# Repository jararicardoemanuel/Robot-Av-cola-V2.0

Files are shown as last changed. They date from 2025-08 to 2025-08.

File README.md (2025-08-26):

<h1 align="center" style="color:brown;">
  🐔🥚Robot Avícola V2.0
</h1>

Proyecto de la Práctica Profesional Supervisada "PPS" en Ingeniería Mecatrónica realizado en la FI-UNLZ.

Es un sistema robótico de 3 GDL para realizar la recolección de huevos en nidos horizontales, tiene implementado un software de procesamiento de imágenes para la detección y localización programado en python utilizando la librería cv2 y un modelo pre-entrenado de roboflow. Se emplea un Sistema IoT para el accionamiento de control, aplicación para el envío de mensajes y recepción a través de "MQTT", además del monitoreo de variables ambientales cómo la temperatura, gas CO2, húmedad.

<p align="center">
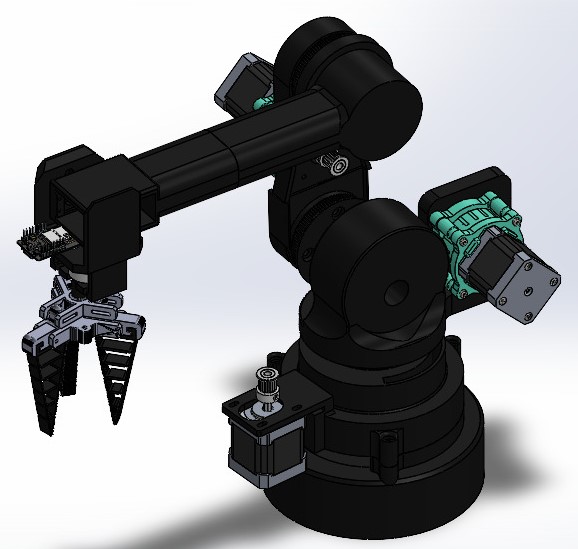
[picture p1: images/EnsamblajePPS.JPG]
  
</p>

## 🟠Tecnologías Aplicadas
• ESP32 - Shield cnc 3 ejes, para el robot se utilizan motores nema 17 con reductor planetario 5:1, motores eléctricos de cc para el carro que lo traslada y sensores de proximidad FC.
• Python - OpenCV, para el diseño de software de detección y calculo de la cinemática inversa.
• Node-RED - MQTT, para el envío y recepción de mensajes, aplicando los nodos se diseño un dashboard de control y monitoreo.
• Sensores de CO₂ MQ135, temperatura y humedad DHT11

## 🟠Prototipo REAL

<p align="center">
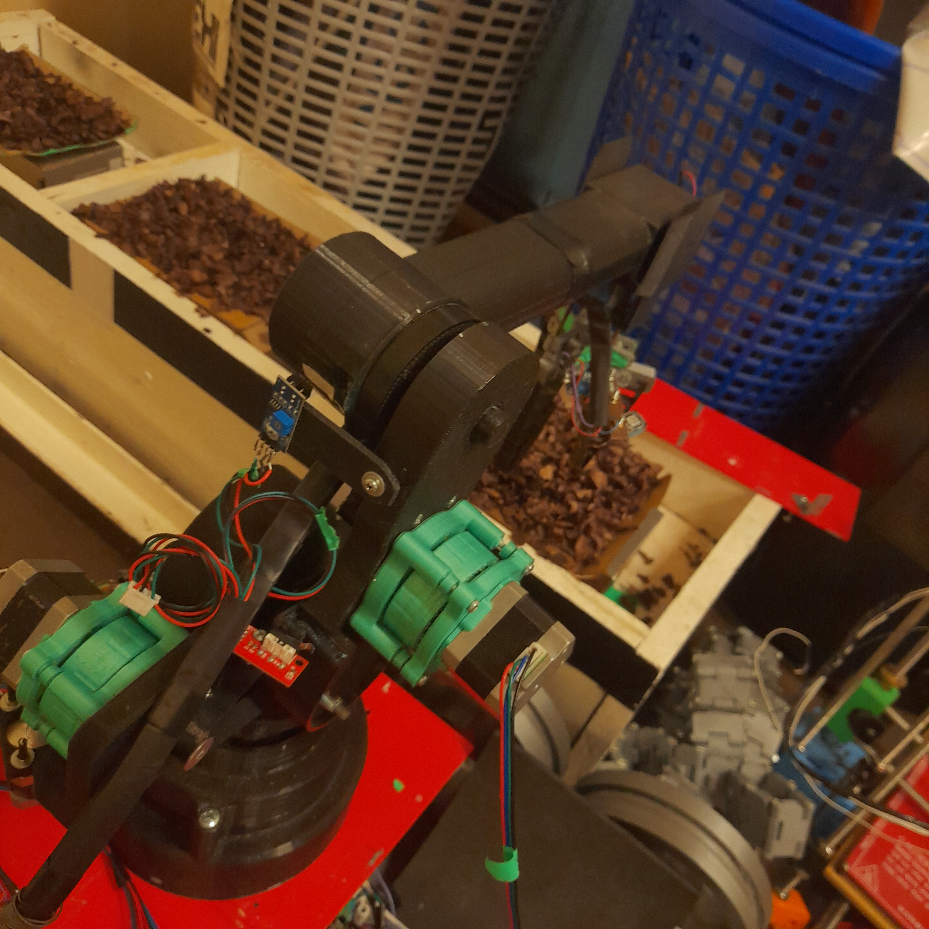
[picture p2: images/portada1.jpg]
  
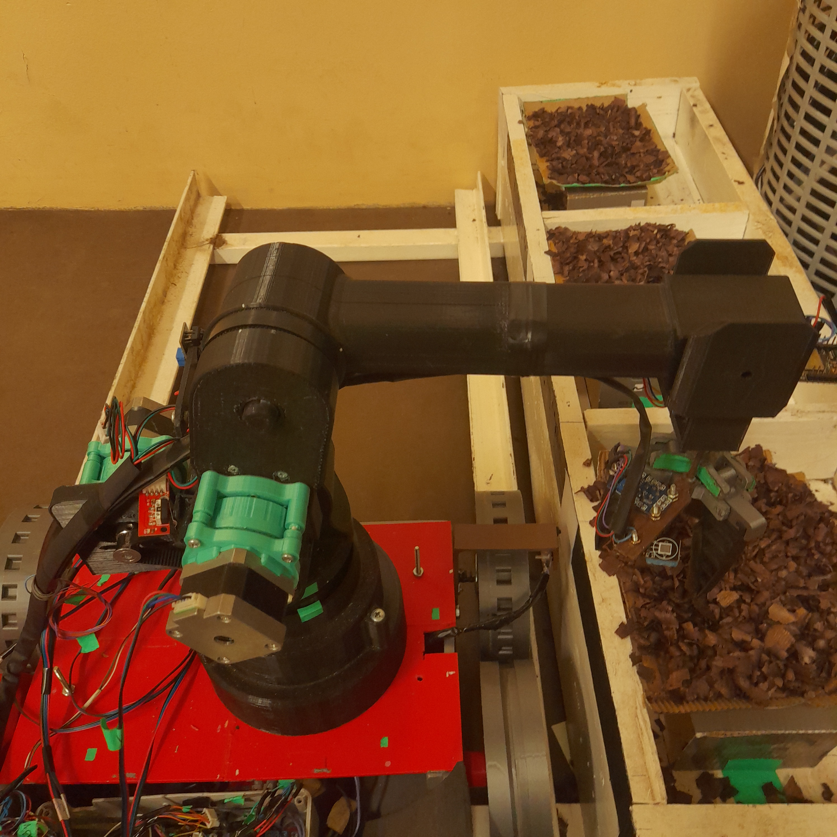
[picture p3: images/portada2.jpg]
  
</p>

## 🟠Procesamiento de Imágenes

Para la detección automática de huevos se utiliza un modelo de visión por computadora entrenado en la plataforma Roboflow. El flujo de trabajo se resume en las siguientes etapas:

### Captura de imagen:
  La cámara ESP32-CAM ubicada en el extremos del codo apuntando hacia abajo captura las imágenes en tiempo real enfocando el nido cubriendo toda la parte donde se ubica el huevo.
  La foto lo comprime en formato JPEG. Este archivo se transfiere a la PC. El resultado de este paso es un archivo ".jpg" accesible en el host.
### Inferencia con el modelo:
  Las imágenes capturadas son enviadas al modelo de Roboflow, el cual aplica un algoritmo de detección de objetos (YOLOv9). Como resultado, se obtiene un conjunto de predicciones que      incluyen:
  Clases detectadas (``huevo'').
  Confianza de detección (probabilidad asociada a la predicción).
  Coordenadas del recuadro:
  (x, y, w, h) donde $x$ e $y$ representan la posición central del objeto, mientras que $w$ y $h$ corresponden al ancho y alto del recuadro.

### Conversión a coordenadas del robot:
  A partir de las coordenadas $(x, y)$ obtenidas de la imagen (resolución de $640 \times 480$ píxeles), se realiza una transformación a coordenadas físicas reales del robot:
  (X_r, Y_r) quedando en función de f (x,y) del sistema
  donde la función $f$ corresponde a la calibración que traduce los píxeles en coordenadas cartesianas, garantizando que el brazo robótico pueda posicionarse correctamente sobre el        huevo.

  • Conversión de píxeles a coordenadas físicas:

En el sistema de visión, las detecciones entregadas por el modelo de Roboflow
se expresan en coordenadas de imagen en píxeles. Para utilizar estos
datos en el control del robot, es necesario transformarlos a coordenadas físicas
(X,Y) medidas en centímetros sobre el plano de trabajo.

En una aproximación simple, se realiza una calibración lineal por
ejes independientes, donde se ajusta un factor de escala y un desplazamiento
(offset) a partir de puntos de referencia medidos experimentalmente:

$$
X = a_x \cdot u + b_x, \qquad
Y = a_y \cdot v + b_y
$$

donde:

  •  \(u,v\): coordenadas en píxeles de la detección
  
  •  \(X,Y\): coordenadas físicas en cm
  
  •  \(a_x, a_y\): factores de conversión (cm/px)
  
  •  \(b_x, b_y\): offsets de calibración

En el prototipo actual se obtuvieron los siguientes valores:

$$
X = (0.0328)\cdot u + 0.5, \qquad
Y = (0.0327)\cdot v + 0.3
$$

### Selección y validación:
  Se consideran válidas únicamente las detecciones cuyo nivel de confianza sea mayor a un umbral predefinido $0.40$. 
    
### Envío al sistema de control:
  Finalmente, con las coordenadas cartesianas corregidas $(X_r, Y_r)$ se calcula la cinemática inversa por método geométrico del robot RRR para luego transmitir los angulos por el protocolo MQTT al controlador del robot para luego ejecutar la secuencia de agarre y recolección.

  La salida del modelo Roboflow
  La predicción para un huevo detectado es el siguiente:
  "predictions": 
      "class": "egg",
      "confidence": 0.89,
      "x": 320,
      "y": 240,
      "width": 50,
      "height": 60
Este resultado indica que se detectó un huevo con una confianza del $0.89$ en la posición $(320, 240)$. Se adjuntan imagenes dónde se observa la localización del objeto y como son transmitidas a través de mqtt.

<p align="center">
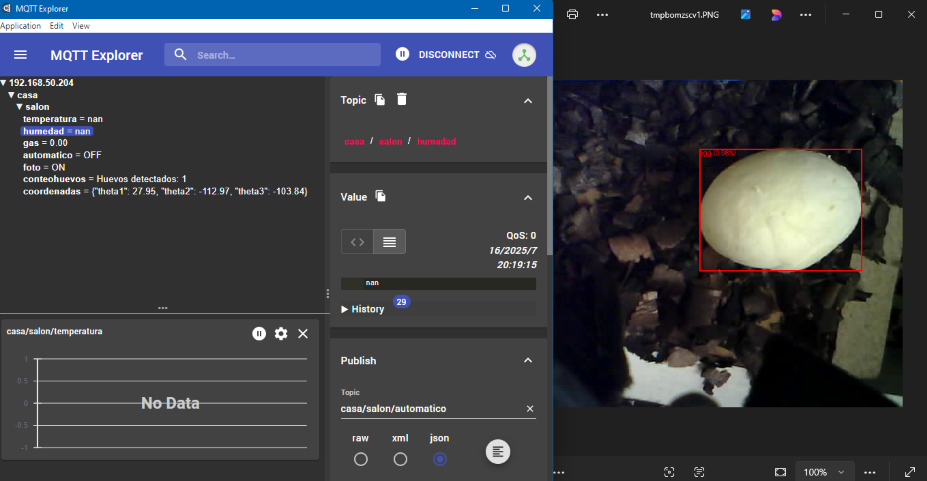
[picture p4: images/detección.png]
  
</p>
<p align="center">
  Vista del robot
</p>

## 🟠Modelo matemático (Cinemática inversa) Robot

En los siguientes ítems se describe el modelo cinemático inverso aplicado al robot de 3GDL por método geométrico.

 🔹 Articulación de la base $$\(\theta_1)$$

Este ángulo se obtiene a partir de la proyección del punto de acción sobre el plano XY.  
Las rotaciones se consideran respecto al eje Z.

$Coordenadas (px, py)$

$$
\theta_1 = 2\arctan\left(\frac{py}{px}\right)
$$

🔹 Articulación del brazo $$\(\theta_2)$$

$$
A_1 = l_1 + l_2 \cos(\theta_3), \quad A_2 = l_2 \sin(\theta_3)
$$

La distancia proyectada sobre el plano XY es:

$$
d_p = p_x \cos(\theta_1) + p_y \sin(\theta_1)
$$

Relaciones trigonométricas:

$$
\sin(\theta_2) = \frac{p'_z A_1 - d_p A_2}{A_1^2 + A_2^2}
$$

$$
\cos(\theta_2) = \frac{d_p A_1 - p'_z A_2}{A_1^2 + A_2^2}
$$

Finalmente:

$$
\theta_2 = 2\arctan\left(\frac{\sin(\theta_2)}{\cos(\theta_2)}\right)
$$

🔹  Articulación del codo $$\(\theta_3)$$

Se ajusta en el plano vertical de la base, considerando la distancia entre el gripper y el extremo del codo.  

Paso1. Se calcula la coordenada corregida en Z:

$$\ p'_z = p_z - b \$$

Paso2. Distancia proyectada:

$$\ D^2 = p_x^2 + p_y^2 + (p'_z)^2 \$$

Paso3. Aplicando la ley de cosenos:

$$\cos(\theta_3) = \frac{D^2 - l_1^2 - l_2^2}{2 l_1 l_2}\$$

Paso4. Ángulo del codo:

$$\theta_3 = 2\arctan\left(\frac{\sqrt{1-\cos^2(\theta_3)}}{\cos(\theta_3)}\right)\$$

Configuración **codo arriba**

• Con estos tres coordenadas articulares $$\(\theta_1, \theta_2, \theta_3)\$$ se obtiene la **configuración del robot** para alcanzar cualquier punto dentro de su espacio de trabajo 17x13cm.

## 🟠Plano Electrónico
Aquí una vista general del diagrama electrónico principal del prototipo:

<p align="center">
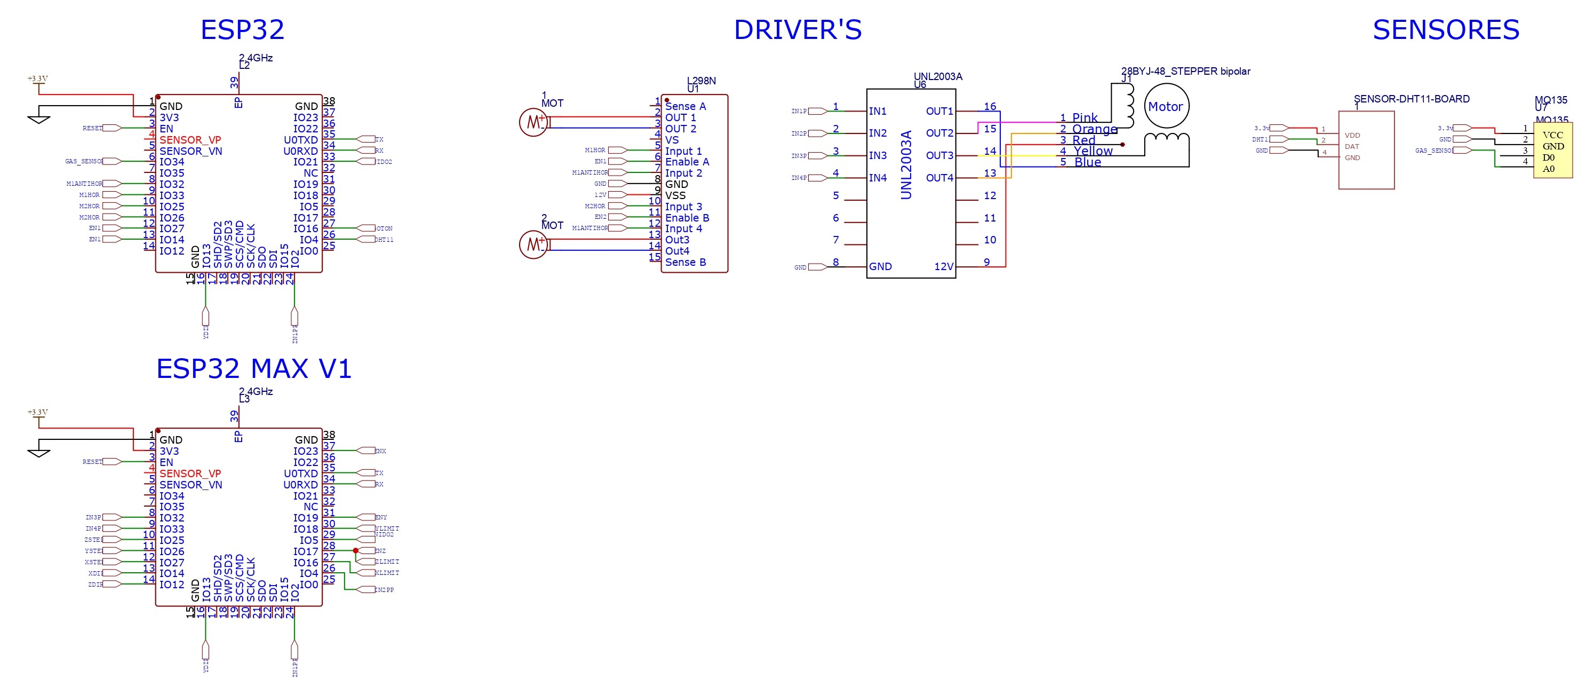
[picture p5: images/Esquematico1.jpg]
  
</p>
<p align="center">
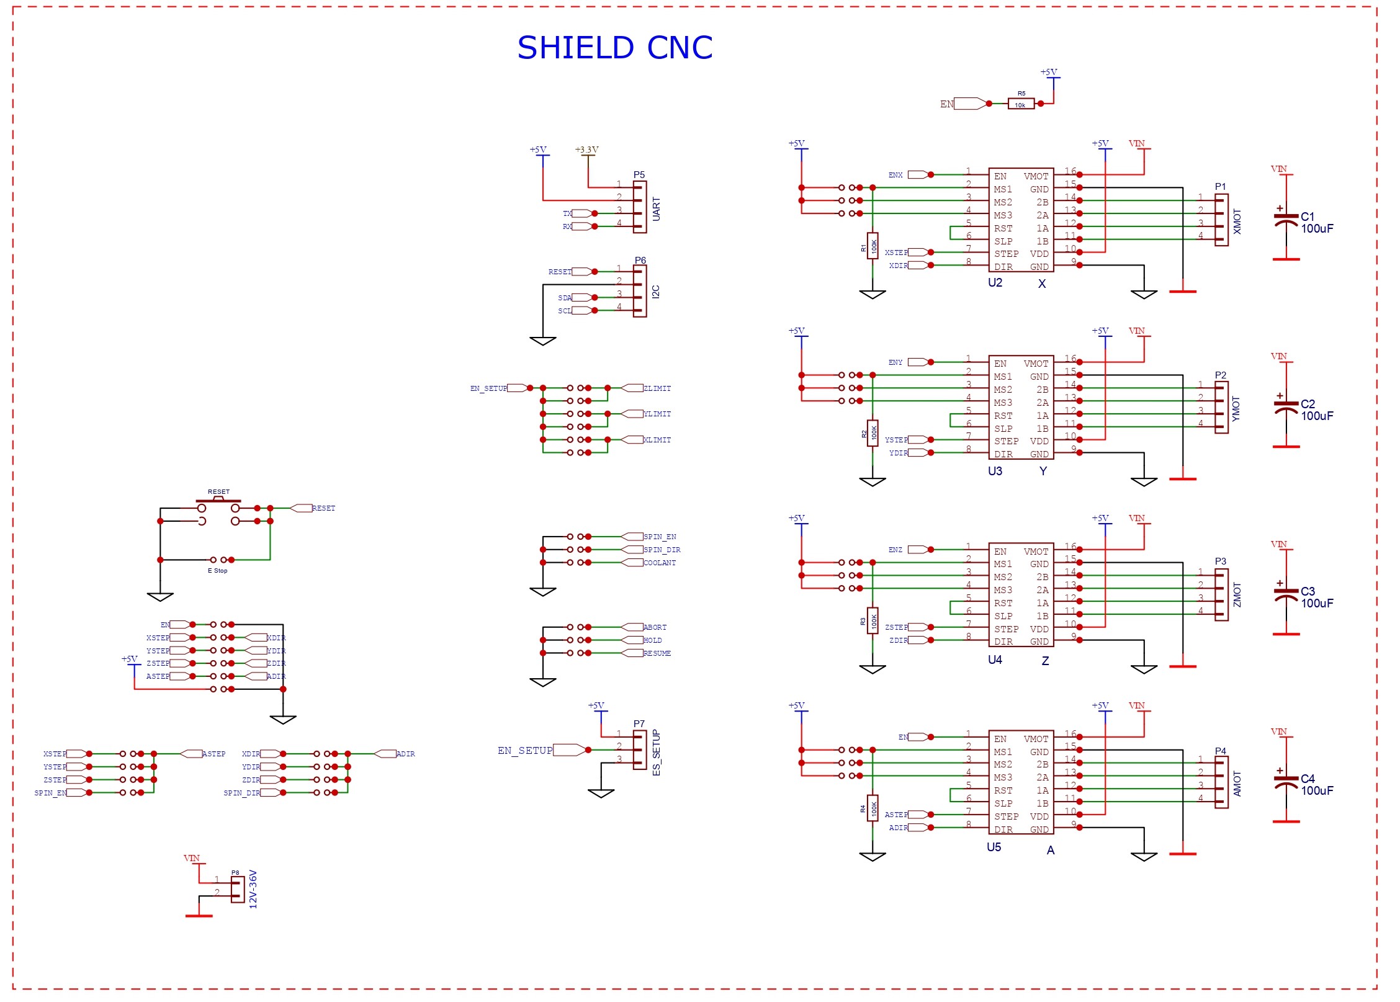
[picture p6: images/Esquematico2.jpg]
  
</p>

## 🟠Planos Mecánicos
Aquí una vista general de los planos del prototipo:

<p align="center">
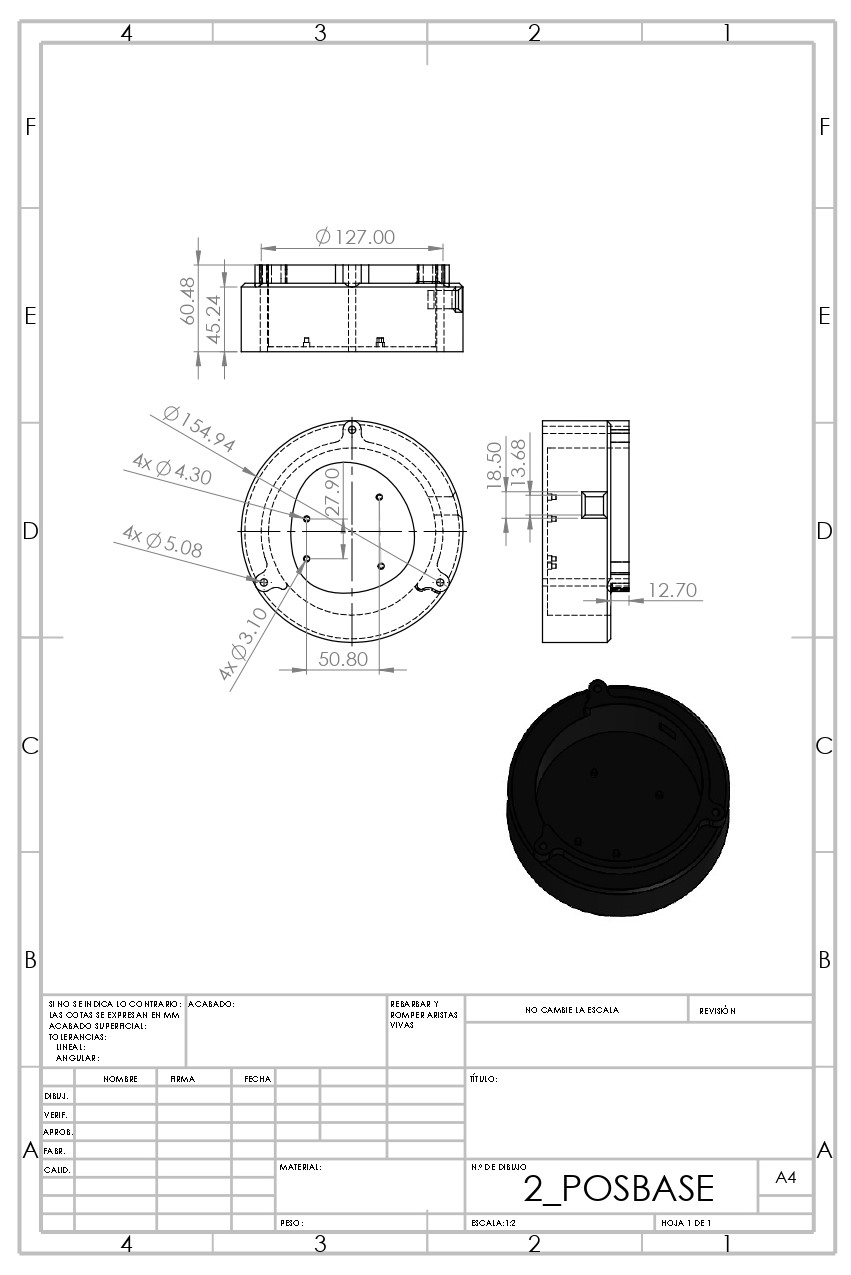
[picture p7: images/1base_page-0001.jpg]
  
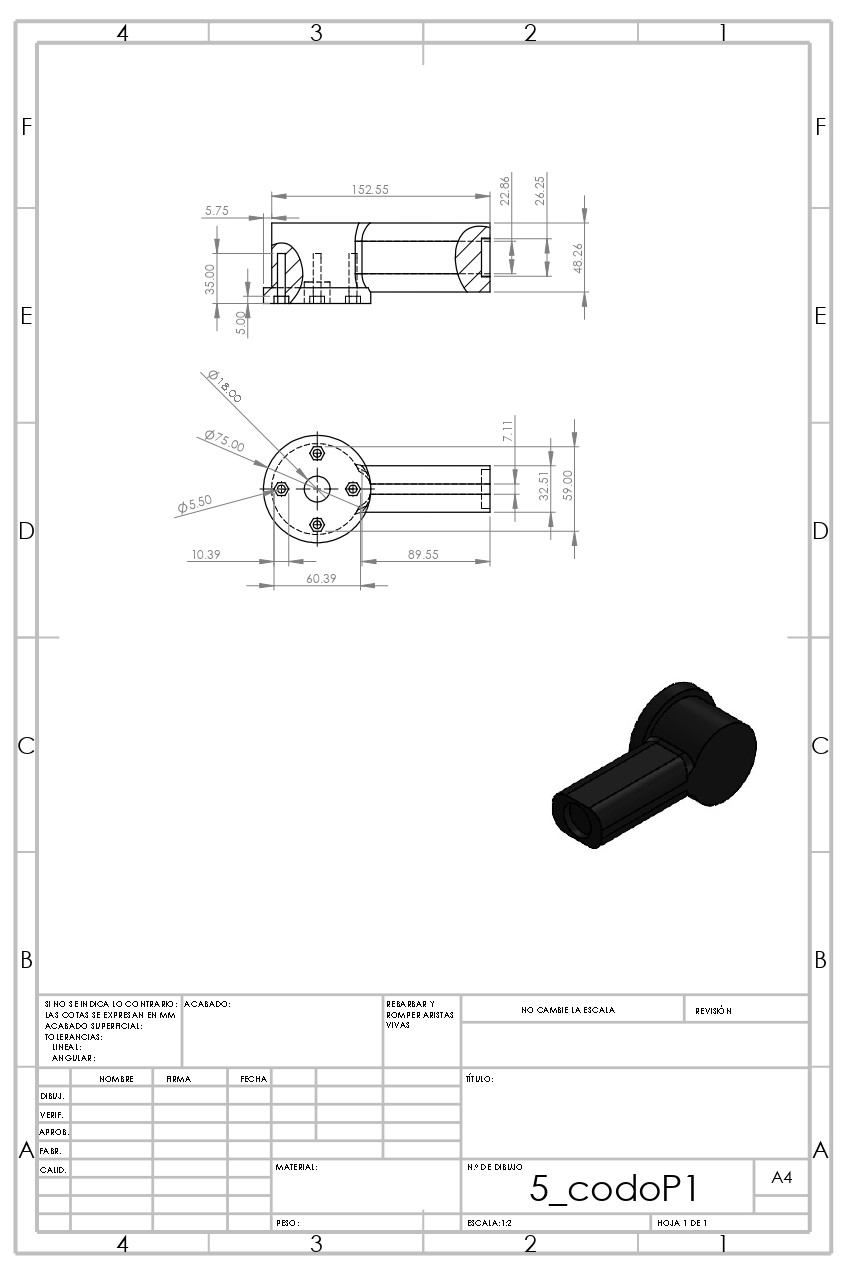
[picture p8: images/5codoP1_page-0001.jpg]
  
</p>

## 🟠Video del Prototipo en funcionamiento

[Link de Google Drive](https://drive.google.com/file/d/1ZrKL6yfj1HvtoRiwAzGiAirnJcBjSen1/view?usp=drive_link)

<p align="center">
  Vista del robot
</p>

## Agradecimiento

Quiero agradecer al profesor de la materia Proyecto Mecatrónico LUKASZEWICZ, Cristian por su acompañamiento durante el desarrollo de este proyecto, el cual constituye una extensión del proyecto final de la carrera. La experiencia me permitió consolidar conocimientos en robótica, procesamiento de imágenes, aplicaciones de softwares de diseño y programación, para así aplicarlos de manera práctica, logrando resultados satisfactorios en la precisión del agarre del objeto gracias a la integración de conceptos fundamentales que se requerían. Este trabajo representa un paso importante en mí proceso de constante aprendizaje, fortaleciendo las bases para seguir avanzando hacia las ciencias aplicadas y la construcción de nuevos desarrollos tecnológicos que me vaya proponiendo. Un fuerte agradecimiento a la FI-UNLZ por permitirme formarme en esta casa de estudios, brindándome oportunidades de crecer en mí formación profesional.

<p align="center">
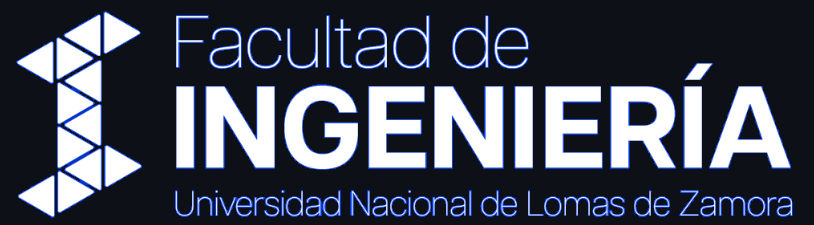
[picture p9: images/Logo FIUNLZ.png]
  
</p>

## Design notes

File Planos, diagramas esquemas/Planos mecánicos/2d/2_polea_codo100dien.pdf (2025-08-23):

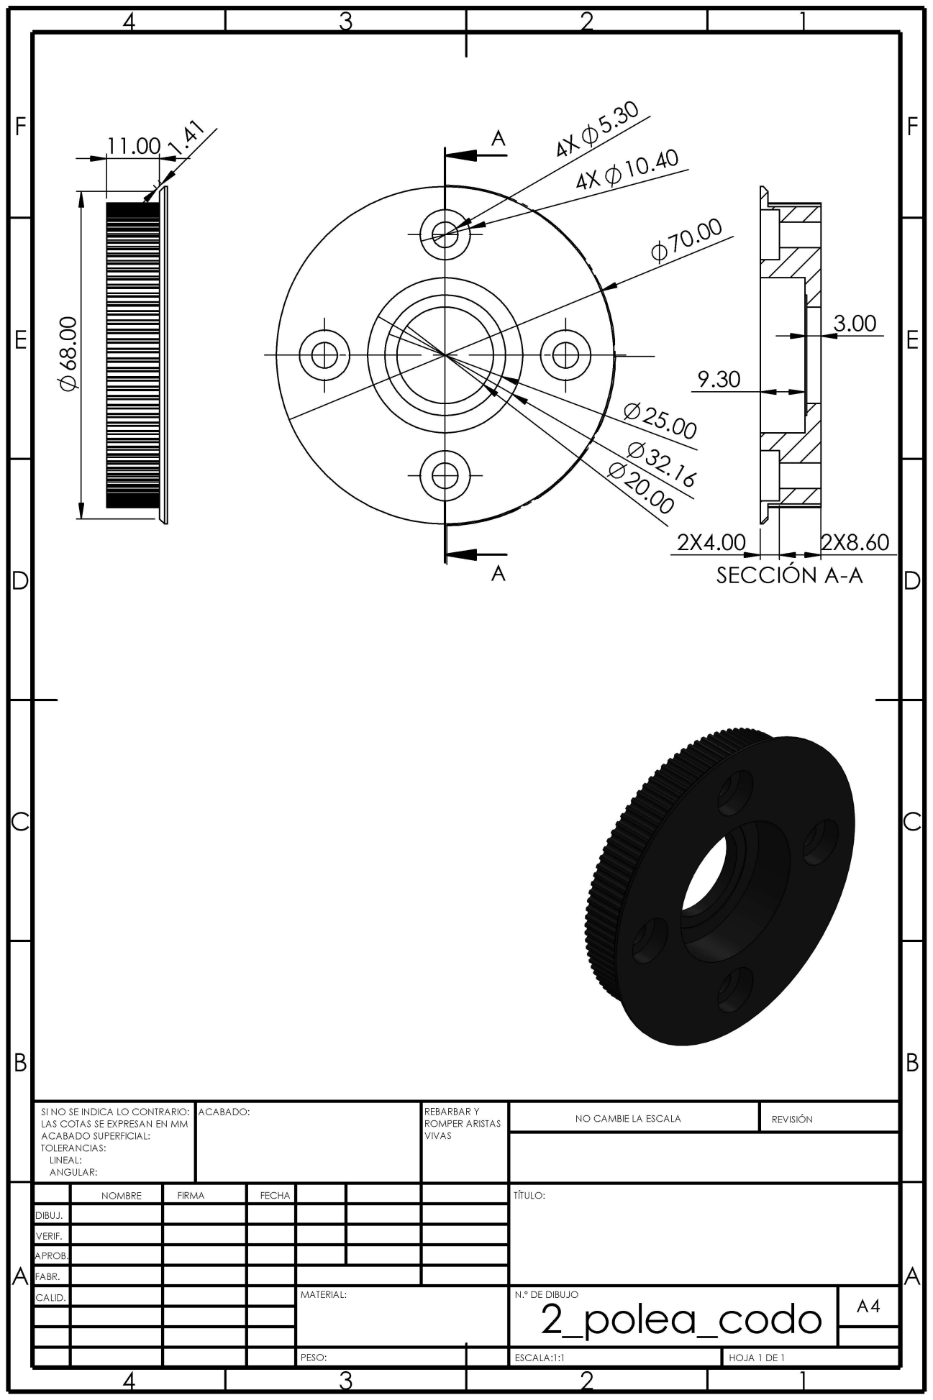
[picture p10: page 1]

Producto SOLIDWORKS Educational. Solo para uso en la enseñanza.

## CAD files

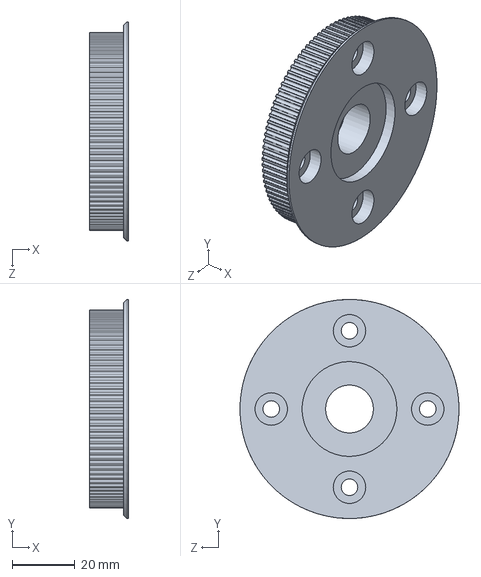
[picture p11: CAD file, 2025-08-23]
Planos, diagramas esquemas/Planos mecánicos/3d/6_polea_brazo.SLDPRT
12.6 x 70.0 x 70.0 mm

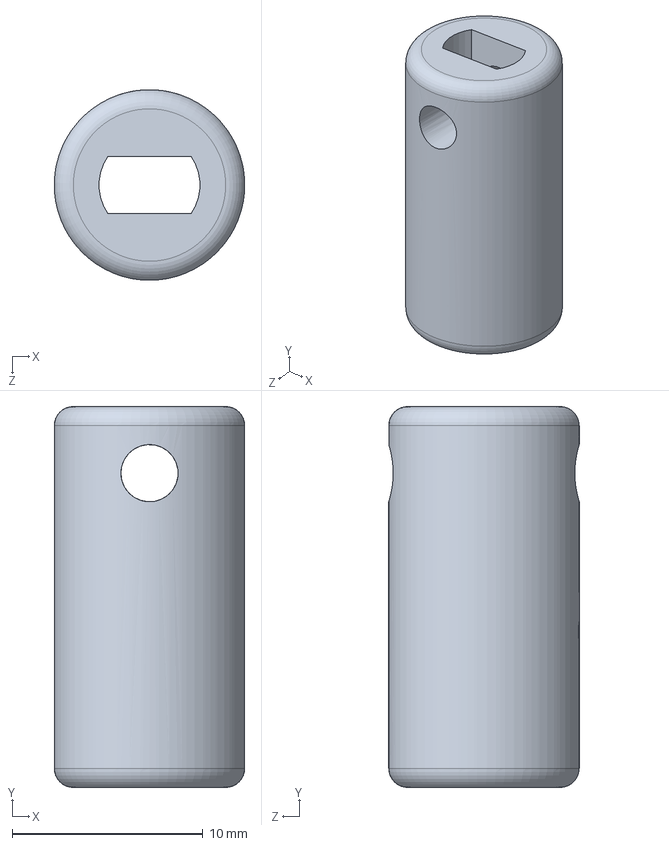
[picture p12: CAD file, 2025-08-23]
Planos, diagramas esquemas/Planos mecánicos/3d/acople PP.SLDPRT
10.00 x 20.0 x 10.0 mm

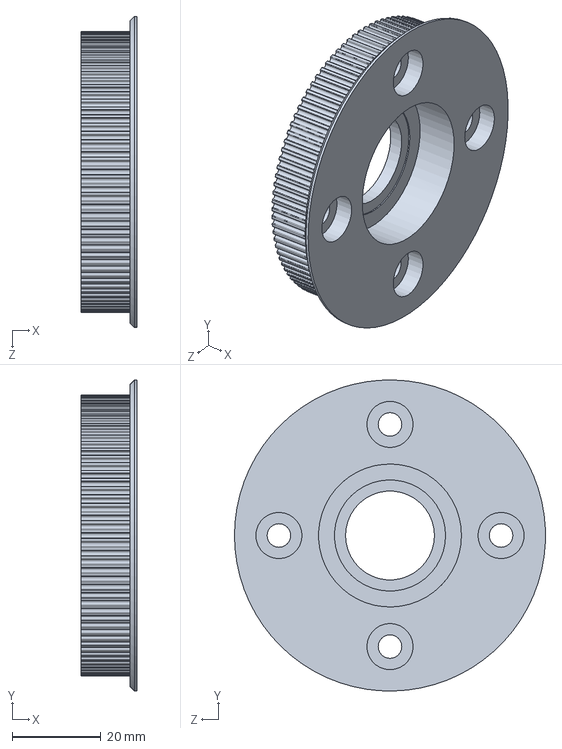
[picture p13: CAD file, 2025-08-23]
Planos, diagramas esquemas/Planos mecánicos/3d/2_polea_codo.SLDPRT
12.6 x 70.0 x 70.0 mm

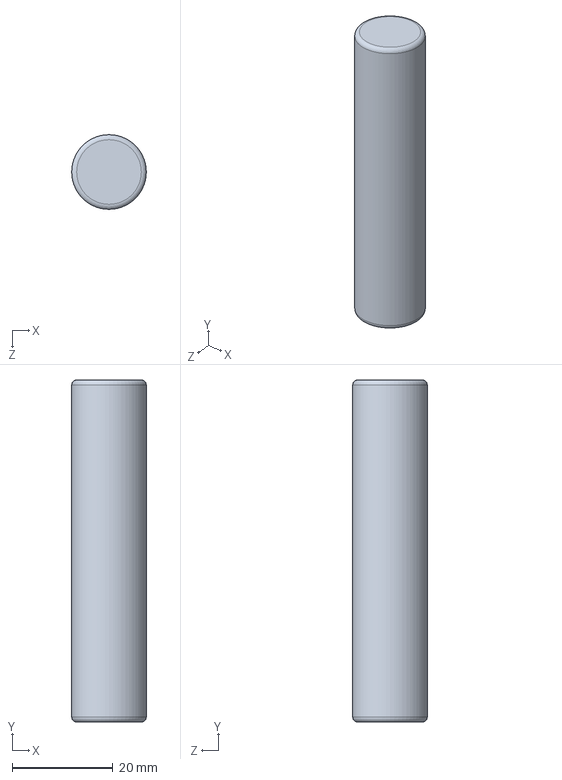
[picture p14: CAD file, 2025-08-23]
Planos, diagramas esquemas/Planos mecánicos/3d/LARGOsemieje_15x68mm - copia.SLDPRT
14.9 x 68.0 x 14.9 mm

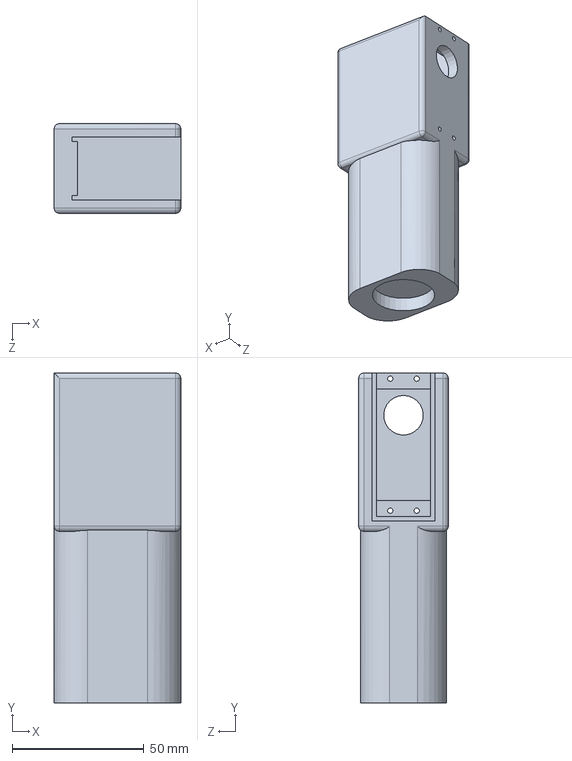
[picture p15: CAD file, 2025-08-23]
Planos, diagramas esquemas/Planos mecánicos/3d/5codoP2.SLDPRT
48.0 x 125.0 x 34.0 mm

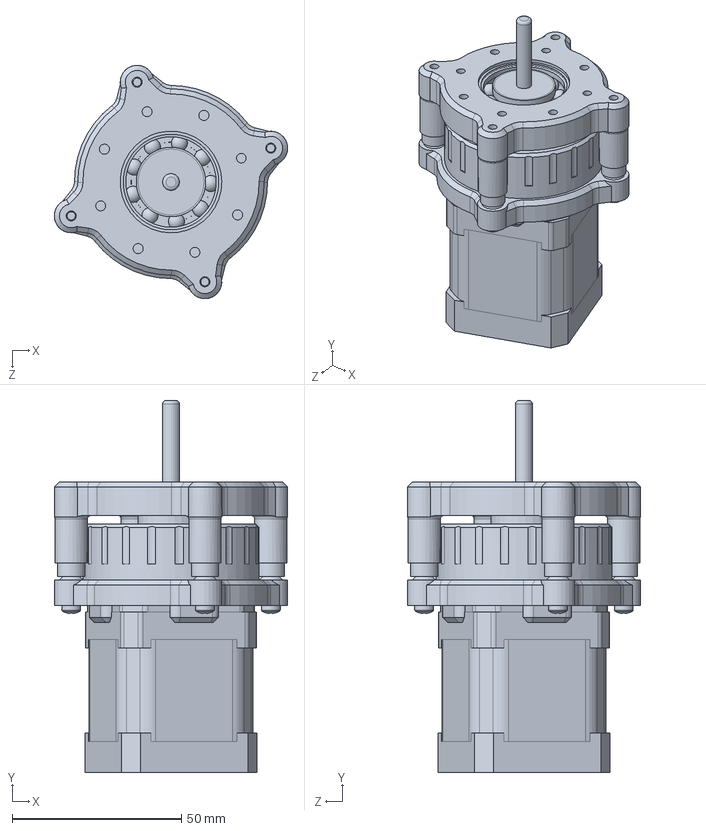
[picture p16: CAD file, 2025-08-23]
Planos, diagramas esquemas/Planos mecánicos/3d/motorreductorV2.SLDPRT
68.9 x 109.8 x 68.9 mm

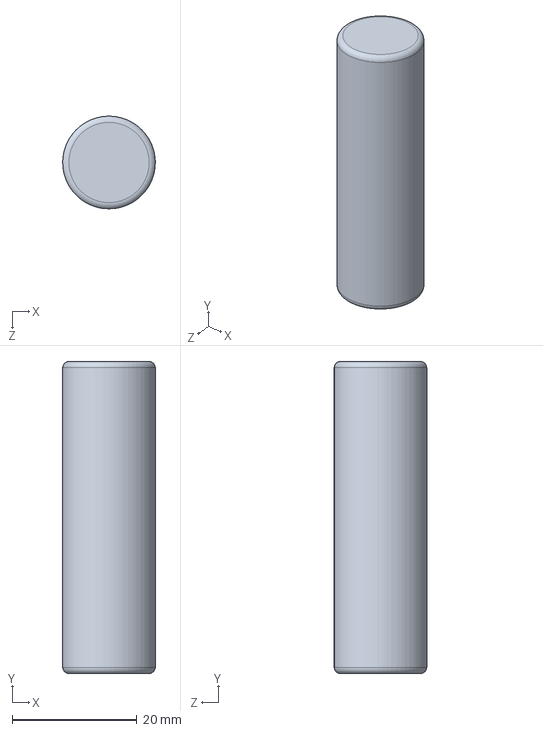
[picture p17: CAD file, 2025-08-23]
Planos, diagramas esquemas/Planos mecánicos/3d/semieje_15x50mm.SLDPRT
14.8 x 50.0 x 14.9 mm

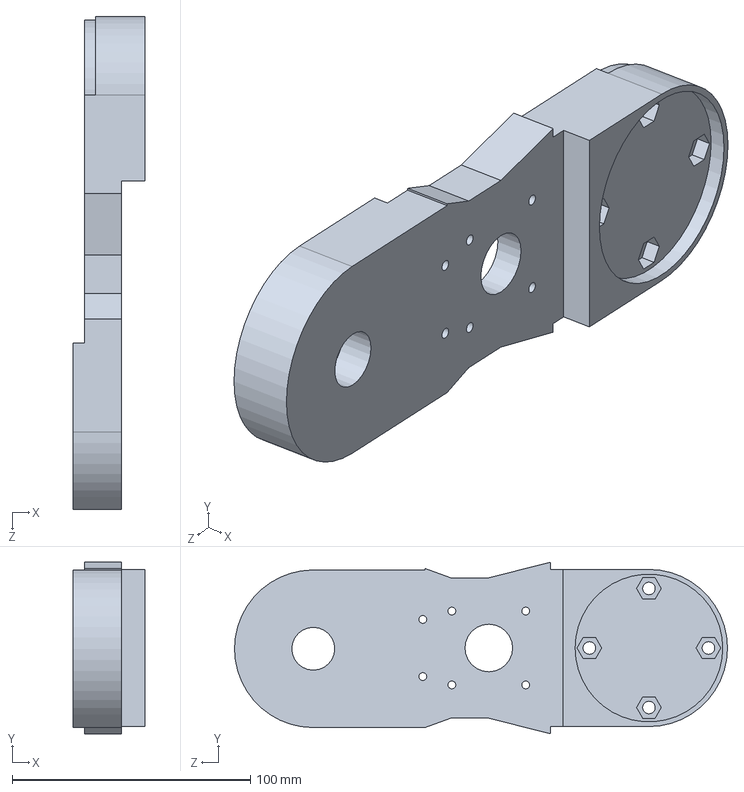
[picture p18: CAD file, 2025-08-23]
Planos, diagramas esquemas/Planos mecánicos/3d/4_BRAZO.SLDPRT
30.4 x 72.0 x 207.0 mm

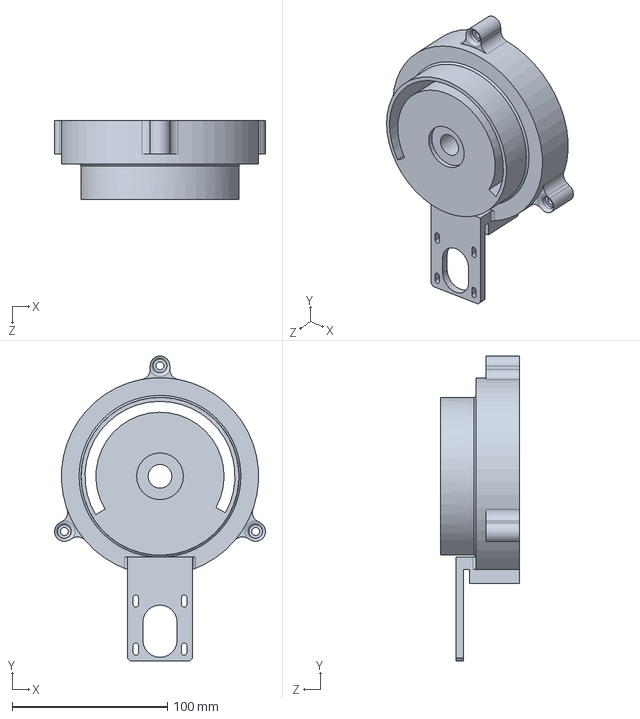
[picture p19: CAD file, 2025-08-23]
Planos, diagramas esquemas/Planos mecánicos/3d/2_POSBASE.SLDPRT
135.9 x 196.4 x 50.8 mm

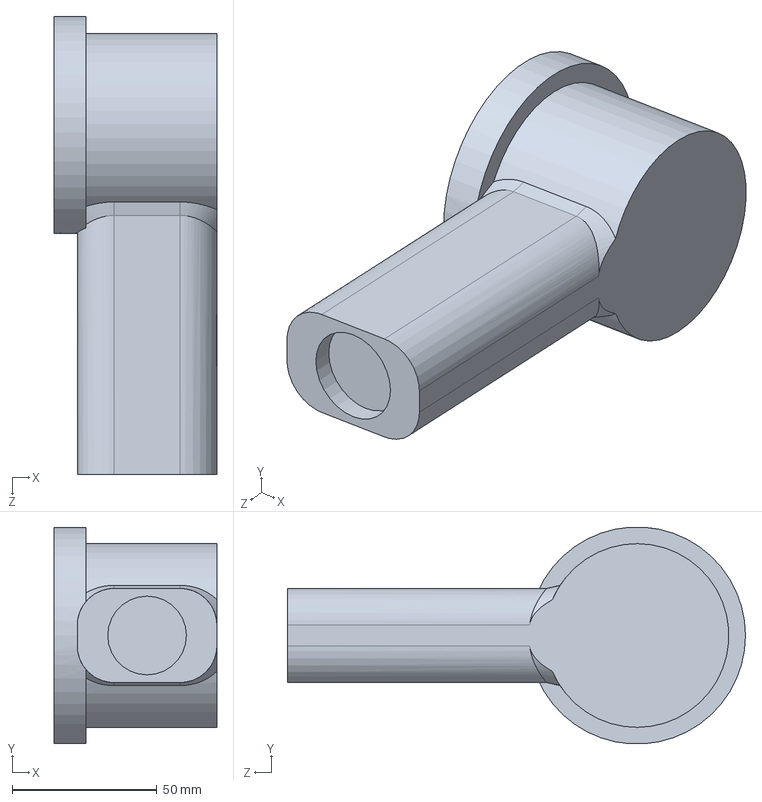
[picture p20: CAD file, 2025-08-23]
Planos, diagramas esquemas/Planos mecánicos/3d/5codoP1.SLDPRT
56.3 x 74.8 x 158.3 mm

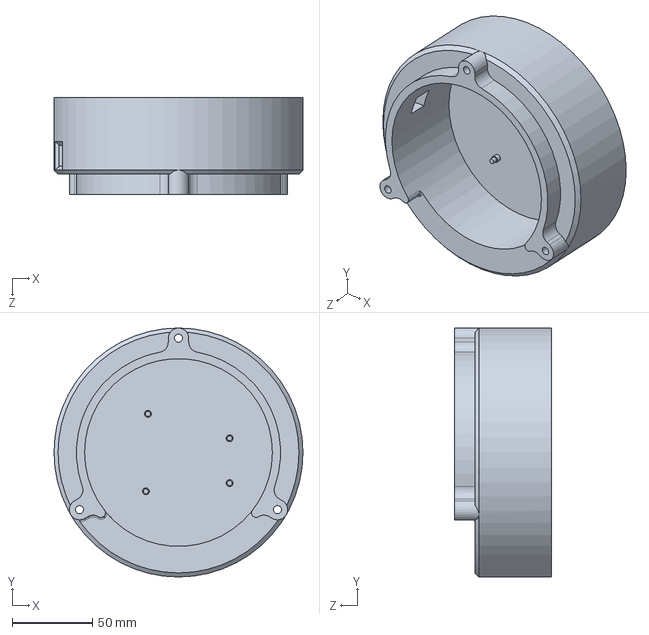
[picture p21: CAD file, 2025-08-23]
Planos, diagramas esquemas/Planos mecánicos/3d/1_BASE.SLDPRT
154.9 x 154.9 x 60.5 mm

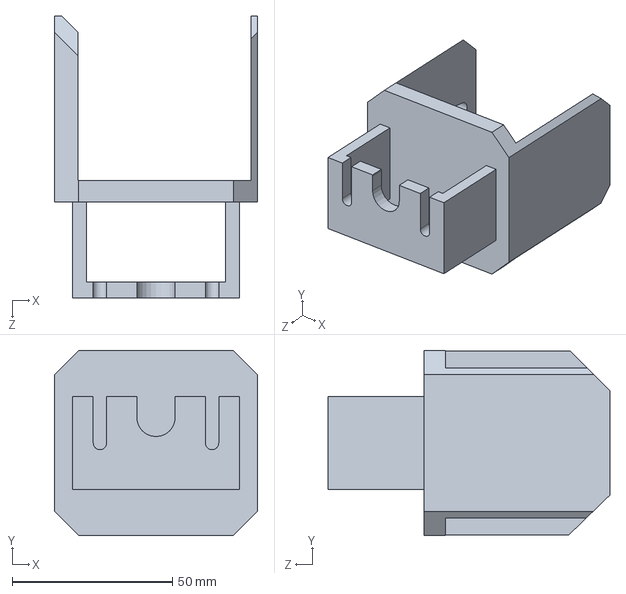
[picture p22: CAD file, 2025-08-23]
Planos, diagramas esquemas/Planos mecánicos/3d/7_MUÑECA.SLDPRT
63.5 x 57.9 x 88.1 mm

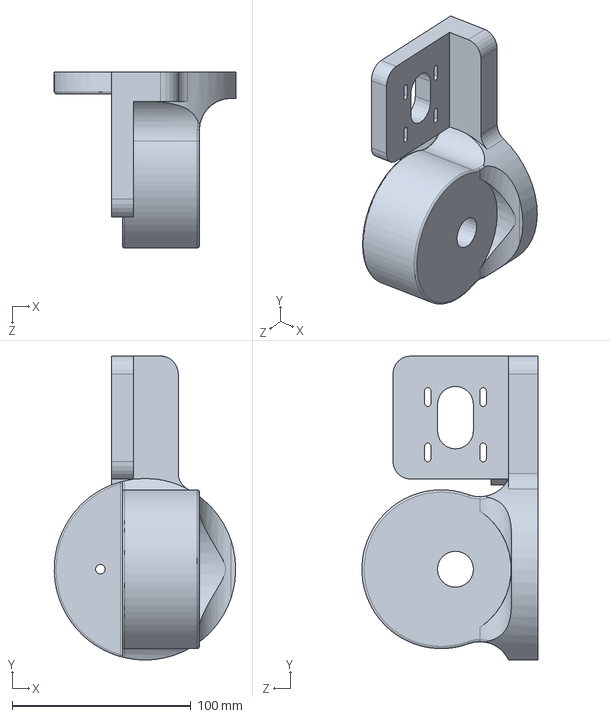
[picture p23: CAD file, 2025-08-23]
Planos, diagramas esquemas/Planos mecánicos/3d/3_CENTRAL.SLDPRT
101.6 x 170.1 x 98.5 mm

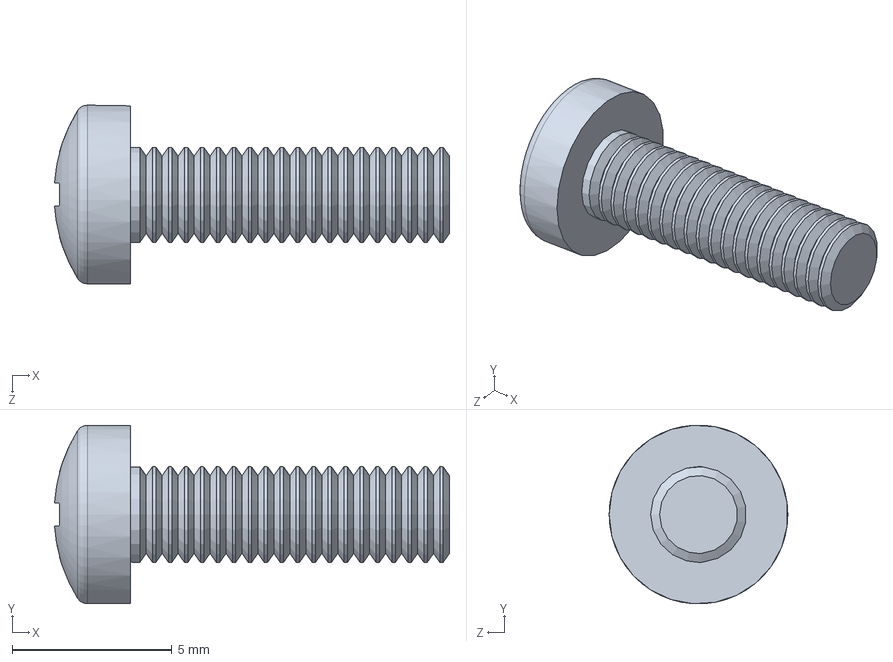
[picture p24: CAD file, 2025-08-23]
Planos, diagramas esquemas/Planos mecánicos/3d/B18.6.7M - M3 x 0.5 x 10 Type I Cross Recessed PHMS --10S.SLDPRT
12.4 x 5.59 x 5.60 mm

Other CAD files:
Planos, diagramas esquemas/Planos mecánicos/3d/GT2 Timing Pulley 20T 10mm - Bore_5mm.SLDASM
Planos, diagramas esquemas/Planos mecánicos/3d/1Toothless pulley 16t gt2.SLDPRT
Planos, diagramas esquemas/Planos mecánicos/3d/B18.6.7M - M3 x 0.5 x 20 Type I Cross Recessed PHMS --20S.SLDPRT
Planos, diagramas esquemas/Planos mecánicos/3d/6_DISCO_CODO.SLDPRT
Planos, diagramas esquemas/Planos mecánicos/2d/1Toothless pulley 16t gt2.SLDDRW
Planos, diagramas esquemas/Planos mecánicos/2d/1_BASE.SLDDRW
Planos, diagramas esquemas/Planos mecánicos/2d/2_POSBASE.SLDDRW
Planos, diagramas esquemas/Planos mecánicos/2d/2_polea_codo.SLDDRW
Planos, diagramas esquemas/Planos mecánicos/2d/3_CENTRAL.SLDDRW
Planos, diagramas esquemas/Planos mecánicos/2d/4_BRAZO.SLDDRW
Planos, diagramas esquemas/Planos mecánicos/2d/5_codoP1.SLDDRW
Planos, diagramas esquemas/Planos mecánicos/2d/5_codoP2.SLDDRW
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

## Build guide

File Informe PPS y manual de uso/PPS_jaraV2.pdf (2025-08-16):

# Universidad Nacional de Lomas de Zamora -

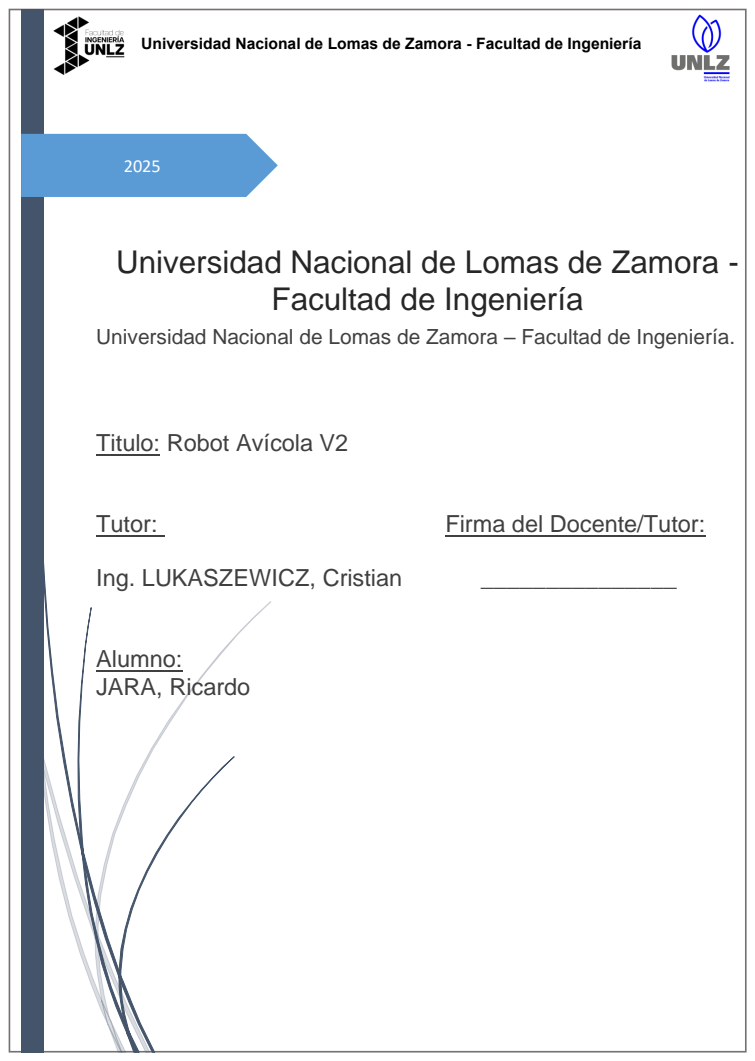
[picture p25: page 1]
Tutor:; Firma del Docente/Tutor:; Ing. LUKASZEWICZ, Cristian; Alumno: JARA, Ricardo

Universidad Nacional de Lomas de Zamora - Facultad de Ingeniería

Facultad de Ingeniería

Universidad Nacional de Lomas de Zamora – Facultad de Ingeniería.

Titulo: Robot Avícola V2

Índice

## Contenido

Reservado a la Facultad para evaluación

Lugar de realización de la PPS

La PPS se llevó a cabo en facultad de ingeniería de la UNLZ y, además otro gran porcentaje del trabajo en mí domicilio particular, dónde tuve a disposición herramientas y máquinas, un lugar adaptado para trabajar en buenas condiciones.
Durante el período he abordado con gran entusiasmo, rigor en el desarrollo y la optimización de un brazo robótico articular RRR de 3 Grados de Libertad (GDL) para el proyecto “ROBOT AVÍCOLA V2”. Este proyecto representó un desafío significativo que me permitió aplicar y expandir mis conocimientos en robótica, automatización y la aplicación de IoT.
Entornos de Trabajo y Recursos Aprovechados:
Las diversas etapas de este proyecto se materializaron en una combinación estratégica de dos entornos de trabajo fundamentales, cada uno aportando recursos y capacidades específicas que fueron cruciales para el éxito del brazo robótico:
Laboratorio de la Facultad: En este espacio se consolidó las pruebas de testeo y validación del sistema. En el laboratorio, tuve acceso a instrumentos de medición de alta precisión, como multímetros, que me permitieron verificar minuciosamente el rendimiento eléctrico/electrónico de cada componente, así como el comportamiento global del brazo. La posibilidad de realizar pruebas bajo condiciones controladas fue indispensable para asegurar la funcionalidad.
Mi Domicilio: Funcionando como una extensión vital del laboratorio, proporcionó un espacio flexible para la fase de desarrollo inicial, ensamblaje y testeos preliminares. Contaba con fuentes de alimentación reguladas, una extensa gama de insumos electrónicos y eléctricos (protoboard, cableado, microcontroladores, etc.), y mis propias herramientas de medición eléctrica portátiles, como multímetros digitales. Esto me facilitó la realización de las primeras pruebas, la depuración de circuitos de control y los ajustes de software en un ambiente más personal. Trabajar en mí casa permitió una iteración rápida de ideas y soluciones, además de probar, simular antes de llevarlo a la realidad, además de gestionar mis tiempos.
Tecnologías y Herramientas Fundamentales Implementadas:
Para el diseño, construcción y programación del brazo robótico, integré diversas tecnologías y herramientas, abarcando desde la concepción virtual hasta el control físico:
Diseño Asistido por Computadora (CAD) y Simulación. Simulación de trayectorias antes de cualquier ensamblaje físico. Esto no solo ahorró tiempo y recursos, sino que también garantizó un diseño más eficiente y seguro. Régimen de Dedicación Horaria:
La constancia fue un pilar en la ejecución de estas PPS. Me dediqué al proyecto de forma ininterrumpida, trabajando cuatro horas diarias durante todos los días de la semana hábil. Este compromiso sostenido me permitió avanzar de manera sistemática, abordar los desafíos conforme surgían y completar el trabajo dentro de los plazos establecidos, asegurando una progresión constante hacia el objetivo final.

Resumen del trabajo realizado

El trabajo realizado en la etapa de la PPS es el diseño, mejora e implementación de un Brazo Robótico Articular RRR de 3 GDL para un Robot Avícola.
Durante mis Prácticas Profesionales Supervisadas (PPS), llevé a cabo una mejora significativa en un robot avícola existente V1. Logré incorporar un sistema robótico completamente nuevo y más robusto. Este proyecto tuvo como objetivo principal optimizar el proceso de recolección de huevos, logrando un mejor control cinemático y una operación más eficiente pasando a una versión Robot Avícola V2.

A continuación, se irán abordando las etapas del trabajo.

Diseño y Mecánica del Brazo Robótico

El inicio del proyecto se centró en la fase mecánica y de diseño del brazo robótico. Realicé un diseño propio de la estructura, optando por una configuración articular RRR de 3 Grados de Libertad. Este diseño fue crucial para garantizar la manipulabilidad de los huevos de forma segura y precisa. La selección de materiales y la definición de las dimensiones de cada eslabón se realizaron pensando en la rigidez estructural y en la capacidad de carga. Cada componente fue cuidadosamente modelado para asegurar movimientos precisos y consistentes.
La siguiente imagen extraída de SolidWorks software CAD del Robot RRR de 3GDL. Para la fabricación del robot se llevó a cabo en la empresa de manera particular, el material adoptado fue el PLA con la configuración de mayor resistencia. El reductor para el motor Paso a Paso también se realizó del mismo material, al contar con piezas muy pequeñas se procedió a imprimir con las mismas características de dureza con densidad de relleno (entre 50%-70%).

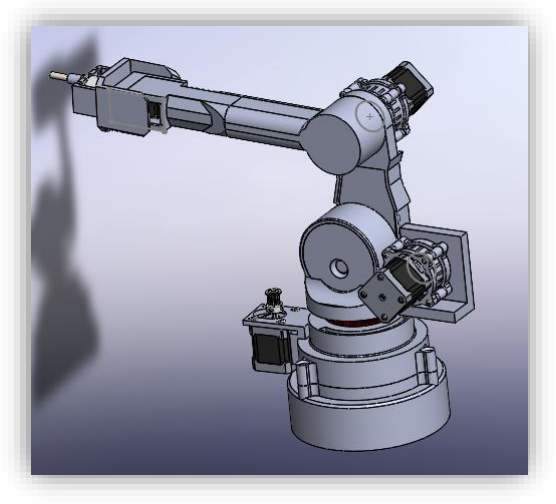
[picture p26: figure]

Ilustración 1 – Vista en perspectiva

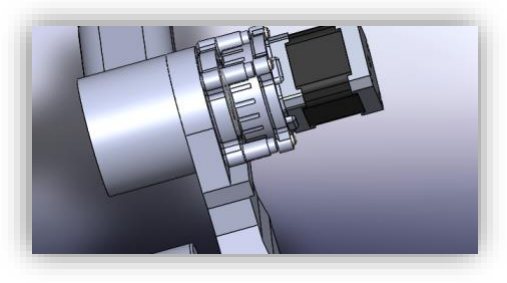
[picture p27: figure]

Ilustración 2 – vista motor PP y su reductor 5:1

Arquitectura Eléctrica y Electrónica

En la parte eléctrica y electrónico, mi trabajo incluyó el diseño detallado de los planos de los circuitos. Estos planos abarcan la interconexión de todos los componentes, desde la alimentación de los motores hasta la comunicación entre los microcontroladores. La arquitectura electrónica fue diseñada para ser modular y escalable, para futuras expansiones y mejoras que se quieran agregar. En cuanto a los microcontroladores, utilicé una combinación estratégica para optimizar las distintas tareas del sistema, fueron adoptadas debido al bajo costo y escalabilidad:

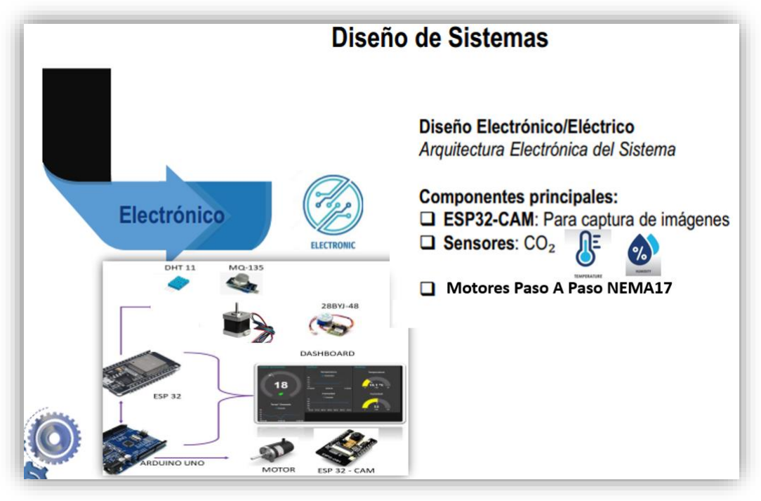
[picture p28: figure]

Componentes principales:

- ESP32-CAM: Dado que este driver integra una cámara muy funcional a los requerimientos que se necesitó. Cuenta con capacidades de controlar su captura hasta poder corregir filtros de imagen. El ESP32 se conecta mediante wifi facilitando así tareas de comunicar software/hardware y envío de manera instantánea al programa de ejecución de proceso e identificación de las imágenes para que pueda procesar el modelo de identificación.
- Arduino Uno: Utilizado para el control directo de los actuadores electromecánicos debido a su robustez y confiabilidad para manejar señales en tiempo real para los motores controlados por PWM. Se utilizaron en total dos, el otro Arduino fue para el control del Brazo.
- ESP32: Utilizado para realizar la lógica del sistema y enlace entre visión artificial, MQTT y, la comunicación UART.
- Motores Paso a Paso NEMA 17 de torque 2.5 Kg.cm, total 3. Para el Gripper se usó un motor PP también 28Byj de torque 1.5 Kg.cm. Motor de CC de 9V 77rpm de corriente continua, con su respectivo controlador de motores L298N.

Desarrollo de Software y Lógica de Control

El desarrollo de software fue una de las etapas más complejas y gratificantes del proyecto, a incluir desde el control de bajo nivel hasta la visión artificial y la comunicación Inter dispositivos, se utilizó diferentes librerías para visión artificial, modelo de detección de huevos en tiempo real, he aplicado, una api para detección de objetos de la página RoboFlow, la página ofrece hacerlo desde la plataforma y en cuestión de segundos obtener el resultado de la detección para luego usarlo en nuestro sistema.
El proceso se basa en:
- Programación en Python implementando el modelo preentrenado de detección.
- Uso de la Liberia de CV2 para calcular la posición exacta del objeto en los ejes coordenados.
- Procesamiento de imágenes en tiempo real, captura y, llamada a la api para hallar la inferencia y porcentaje de confiabilidad del modelo de escala 0 a 1.
- Uso del protocolo de publicación y suscripción de mensajería MQTT para enviar las coordenadas articulares para mover el robot.

- Calculo de la cinemática inversa a partir del modelo matemático de la cinemática directa para un robot de 3 grados de libertad, para hallar los ángulos de las articulaciones.

En la siguiente imagen se observa a modo ilustración las diferentes tecnologías utilizadas.

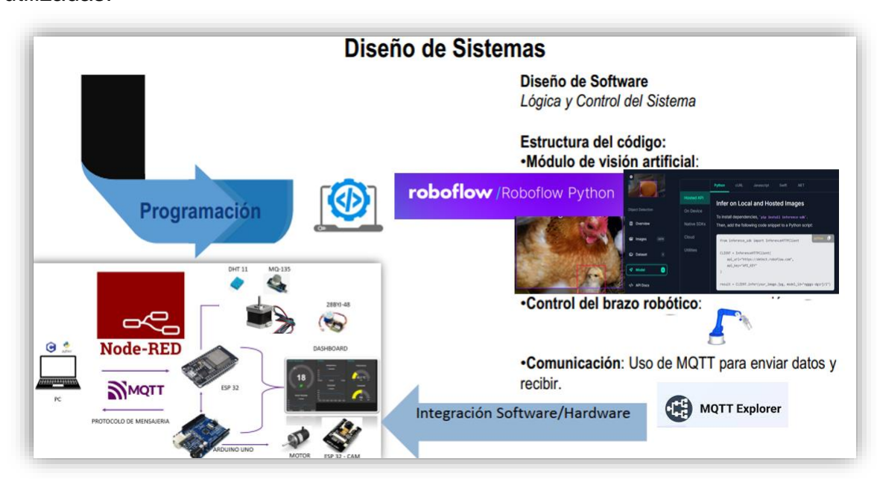
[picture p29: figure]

Diseño | de | un | Dashboard | para | secuencia | de | funcionamiento | en
automático/Manual, se implementó con el objetivo de maniobrar desde aquí de manera visual e intuitiva, se observa el control de temperatura, humedad, gas CO2, esto es visualizada en tiempo real para que el operador que este a su cargo pueda tener en todo momento las condiciones de habitad de las ponedoras.

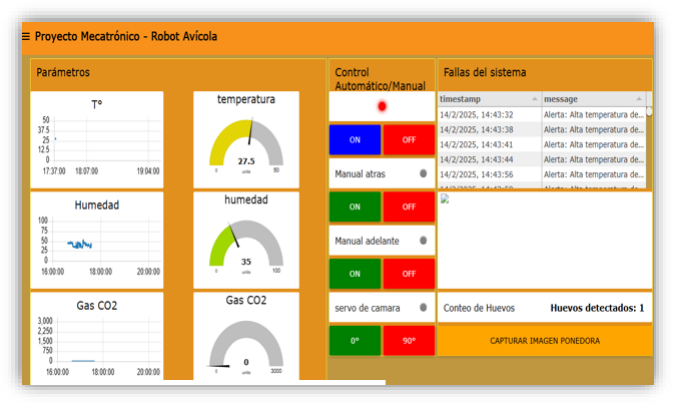
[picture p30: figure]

Control de Actuadores y Sensores

Para el control de los actuadores y sensores, programé el Arduino Uno utilizando lenguaje C (entorno Arduino IDE). Aquí implementado:
La lógica para el control a lazo abierto de los motores paso a paso NEMA 17. Desarrollé algoritmos para generar los pulsos y la secuencia de pasos necesarios para mover cada una de las tres articulaciones del brazo de forma precisa. Esto incluyó la implementación de perfiles de velocidad y aceleración para lograr movimientos suaves.
La lectura y procesamiento de los sensores de fin de carrera utilizados para el homing (referenciado inicial) del brazo.

Sensores utilizados fueron:

- Sensores de Humedad y temperatura DHT11
- Sensor de Gas co2 MQ135
- Sensor de proximidad infrarrojo para seguidor de línea y FC1 robot.

Metodología y Entorno de Trabajo

El desarrollo de este proyecto siguió una metodología estructurada. Las pruebas de testeo exhaustivas se realizaron donde tuve acceso a instrumentos de medición de precisión que me permitieron validar cada aspecto del diseño eléctrico, así como la exactitud de los movimientos del brazo.
Además, para las fases de diseño, realicé simulaciones de los movimientos utilizando herramientas de diseño CAD. Esto me permitió validar la cinemática y la viabilidad del diseño antes de la construcción física, minimizando errores.

El horario de dedicación fue constante: trabajé cuatro horas diarias durante los días de la semana, lo que me permitió avanzar de forma sostenida hasta la culminación del proyecto.

La cinemática inversa es una herramienta fundamental en robótica para determinar los valores articulares que debe adoptar un manipulador para alcanzar una posición y orientación deseada en el espacio de trabajo. En este proyecto, se implementó un modelo de cinemática inversa para un robot antropomórfico con tres grados de libertad (3GDL), del tipo RRR (Revoluta-Revoluta-Revoluta), conformado por tres articulaciones rotacionales y tres eslabones.

La problemática a solucionar era que el efector final del brazo pueda llegar al objeto de manera eficiente, las coordenadas cartesianas que se obtuvieron fueron tomadas por la cámara en lo que respecta el eje x e y, se fue calibrando teniendo en cuenta la perspectiva perpendicular, aplicando una toma hacia abajo, además de lograr corroborar con medición de cinta métrica para ir calibrando y ajustando el error de medición que se tenía.
Se tuvieron en cuenta todos los datos del robot.
- Base de altura b, desde el plano base hasta la primera articulación rotacional.
- Eslabón l1 correspondiente al brazo.
- Eslabón l2 correspondiente al antebrazo.

El objetivo fue hallar las coordenadas articulares θ1 θ2 θ3 que permitan posicionar de forma correcta el extremo del robot.

Calculo de los Ángulos articulares.

- Articulación de la base θ1
Este ángulo se calcula directamente a partir de la proyección del punto de acción sobre el eje XY. Cabe aclarar que las rotaciones son en sentido del eje Z.
θ1 = tg

−12(py/px)
Este valor determina cuanto debemos rotar el eslabón de la base, lo cual orienta un eje a la posición final del objetivo.
- Articulación del codo θ3
Se ajusta la coordenada en el plano vertical de la base, eso se hace por software debido al punto de acción entre el gripper y el extremo del codo. p

′
z = pz − b
Luego aplicar algoritmo matemático para hallar las proyecciones, considerando la distancia al punto objetivo.
D

2 = pz

2 + py

2 + (p′z
)

2

Cos(θ3

) =

D

2 − l1

2 − l2

2
2l1l2

θ3 = tg

−12(√1 − cos²(θ3
) / cos(θ3

))
En este caso se dejó la configuración de codo arriba.
- Articulación del codo θ2
Conocido el ángulo de la articulación tres del codo, se procede a calcular la del brazo.
A1 = l1 + l2 cos(θ3

) , A2 = l2sen(θ3

)

Podemos hallar la distancia proyectada sobre el plano XY:

dp = px cos(θ1

) + py sen(θ1

)
Resolvemos y obtenemos las relaciones:

sen(θ2

) =

p′zA1 − dpA2
A1

2 + A2

2

cos(θ2

) =

dpA1 − p′zA2
A1

2 + A2

2

θ2 = tg

−12(senθ2/ cos(θ2
))

La segunda parte se basó en convertir a pasos los ángulos las articulaciones.

Una vez obtenidos los valores articulares en grados, se convierten a pasos para ser enviados a los motores PP. Esta conversión se realiza en función de la resolución del motor a los pasos por vuelta y del mecanismo de transmisión.

Pasos =

θi

. Pasos por vuelta
360°
Tener en cuenta el reductor del brazo y codo 5:1, esto se traduce en multiplicar los pasos obtenidos por cinco. Para la base se usó direct drive debido a la menor fuerza que puede ejercer.

Este proceso permite controlar el actuador con precisión, asegurando que el efector final se desplace al punto deseado dentro del espacio de trabajo del robot.

Luego de obtener las coordenadas articulares estos son enviados por MQTT al ESP32 y, de este último por comunicación UART serial al Arduino uno Shield 3D CNC que controla los motores PP de las articulaciones.

Conclusión

De cara al futuro, la experiencia con este brazo robótico me ha abierto un sinfín de posibilidades. La capacidad de integrar sistemas de visión por computadora, control cinemático y comunicación entre diferentes microcontroladores, me demuestra que estos conocimientos son altamente transferibles. Podríamos implementar estos sistemas no sólo en la industria avícola, sino también en lo que es la automatización en general, dónde la robótica precisa y autónoma es indispensable. Esto nos permite expandir nuestros conocimientos y aplicar soluciones de ingeniería a problemas complejos en diversos sectores.

La realización de este proyecto en el marco de mis Prácticas Profesionales Supervisadas ha marcado en mi desarrollo, tanto personal como profesional. Me ha permitido consolidar los conocimientos adquiridos a lo largo de la carrera y, lo que es más importante, me ha preparado para los desafíos que el futuro me depara en el ámbito de la ingeniería.
Este trabajo representó la oportunidad perfecta para comprender que la facultad me ha brindado las herramientas básicas para poder construir hacía adelante. Demostramos que la teoría es la base, pero la verdadera formación ocurre al enfrentar problemas reales. El desarrollo del brazo robótico avícola no solo puso a prueba mis habilidades técnicas, sino que también me exigió una serie de competencias blandas esenciales.

He aprendido la vital importancia de la constancia y la disciplina para alcanzar los objetivos propuestos. Hubo momentos de frustración y complejidad, pero la persistencia diaria, trabajando metódicamente y lo más organizado posible, fue lo que me permitió superar cada obstáculo. De cada error, extrajo una valiosa lección; aprenderá a identificarlos, analizarlos y salir adelante, transformando cada tropiezo en una oportunidad de mejora y aprendizaje.

Anexo de Planos
Plano electrónico/Eléctrico

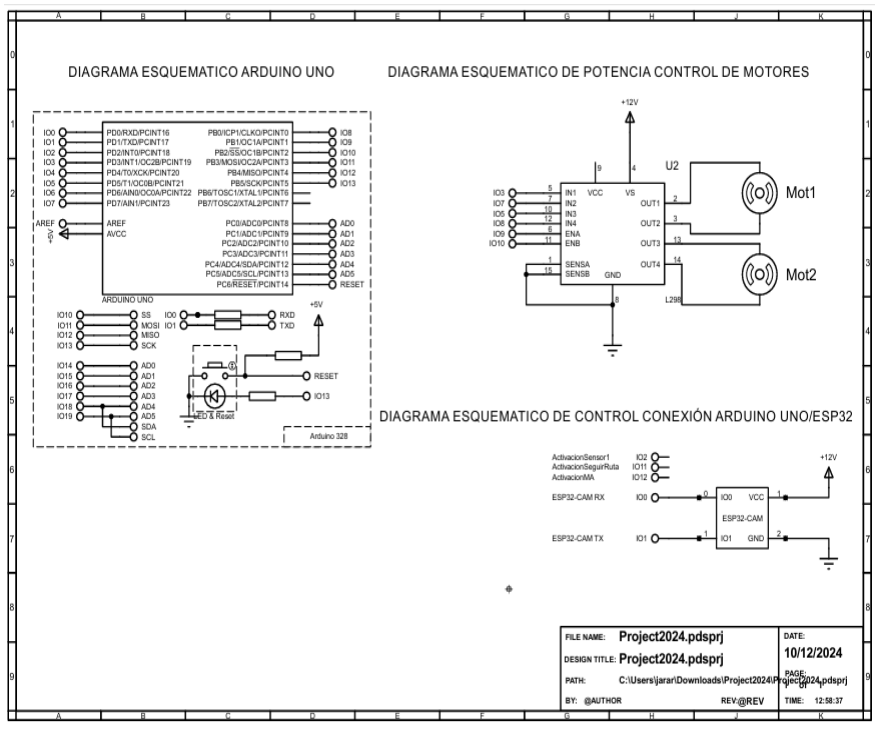
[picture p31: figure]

Plano Eléctrico/Electrónico

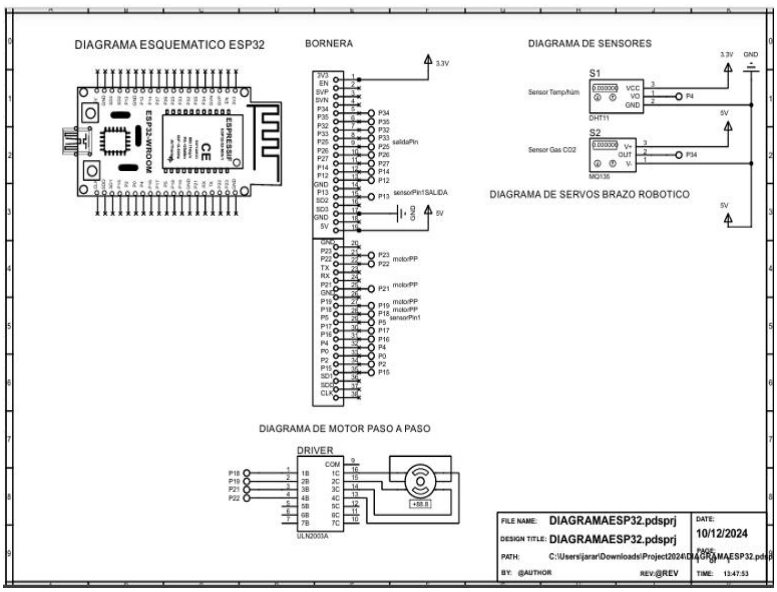
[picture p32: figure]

Se anexa el plano 3D, driver para el control de motores paso a paso de las articulaciones del robot.

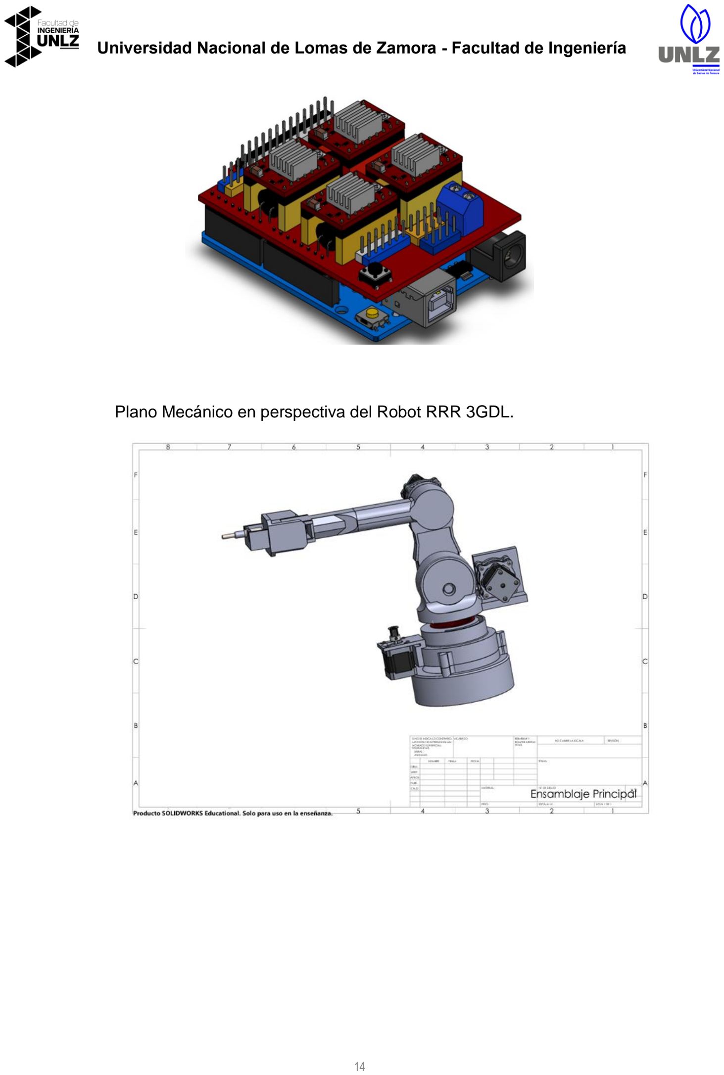
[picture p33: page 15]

Plano Mecánico en perspectiva del Robot RRR 3GDL.

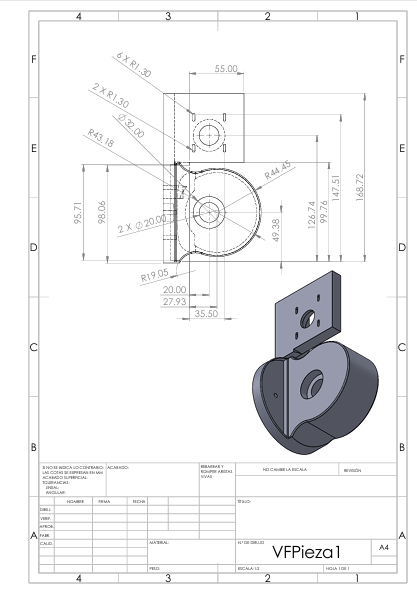
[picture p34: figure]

Adjunto planos. El completo está en el GIT del proyecto.

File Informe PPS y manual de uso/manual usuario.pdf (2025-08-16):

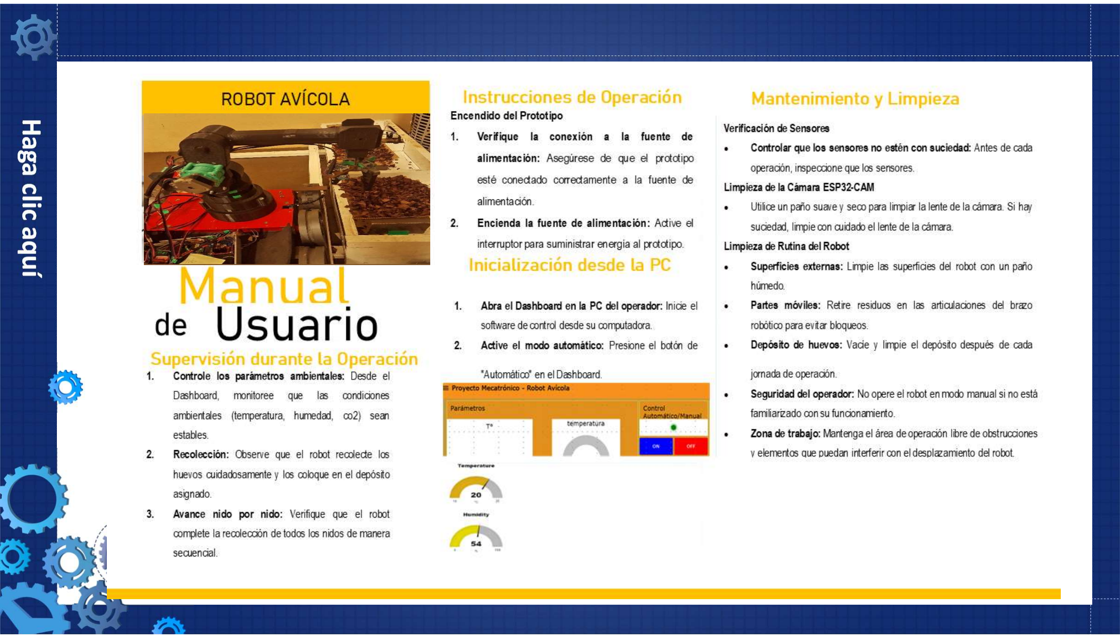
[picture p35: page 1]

Haga clic aquí

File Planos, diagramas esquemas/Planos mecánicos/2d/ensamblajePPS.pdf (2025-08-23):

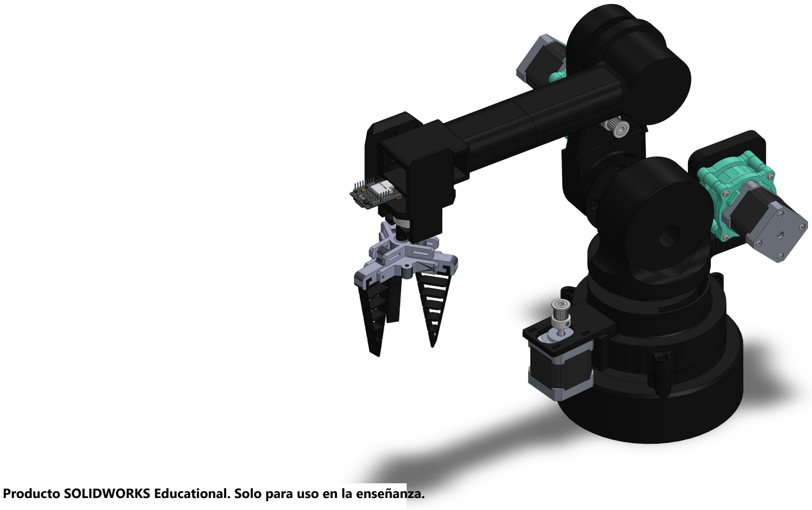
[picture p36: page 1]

Producto SOLIDWORKS Educational. Solo para uso en la enseñanza.

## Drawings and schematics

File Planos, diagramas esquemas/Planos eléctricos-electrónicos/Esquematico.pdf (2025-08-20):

# L2EP 39

DRIVER'S | SENSORES

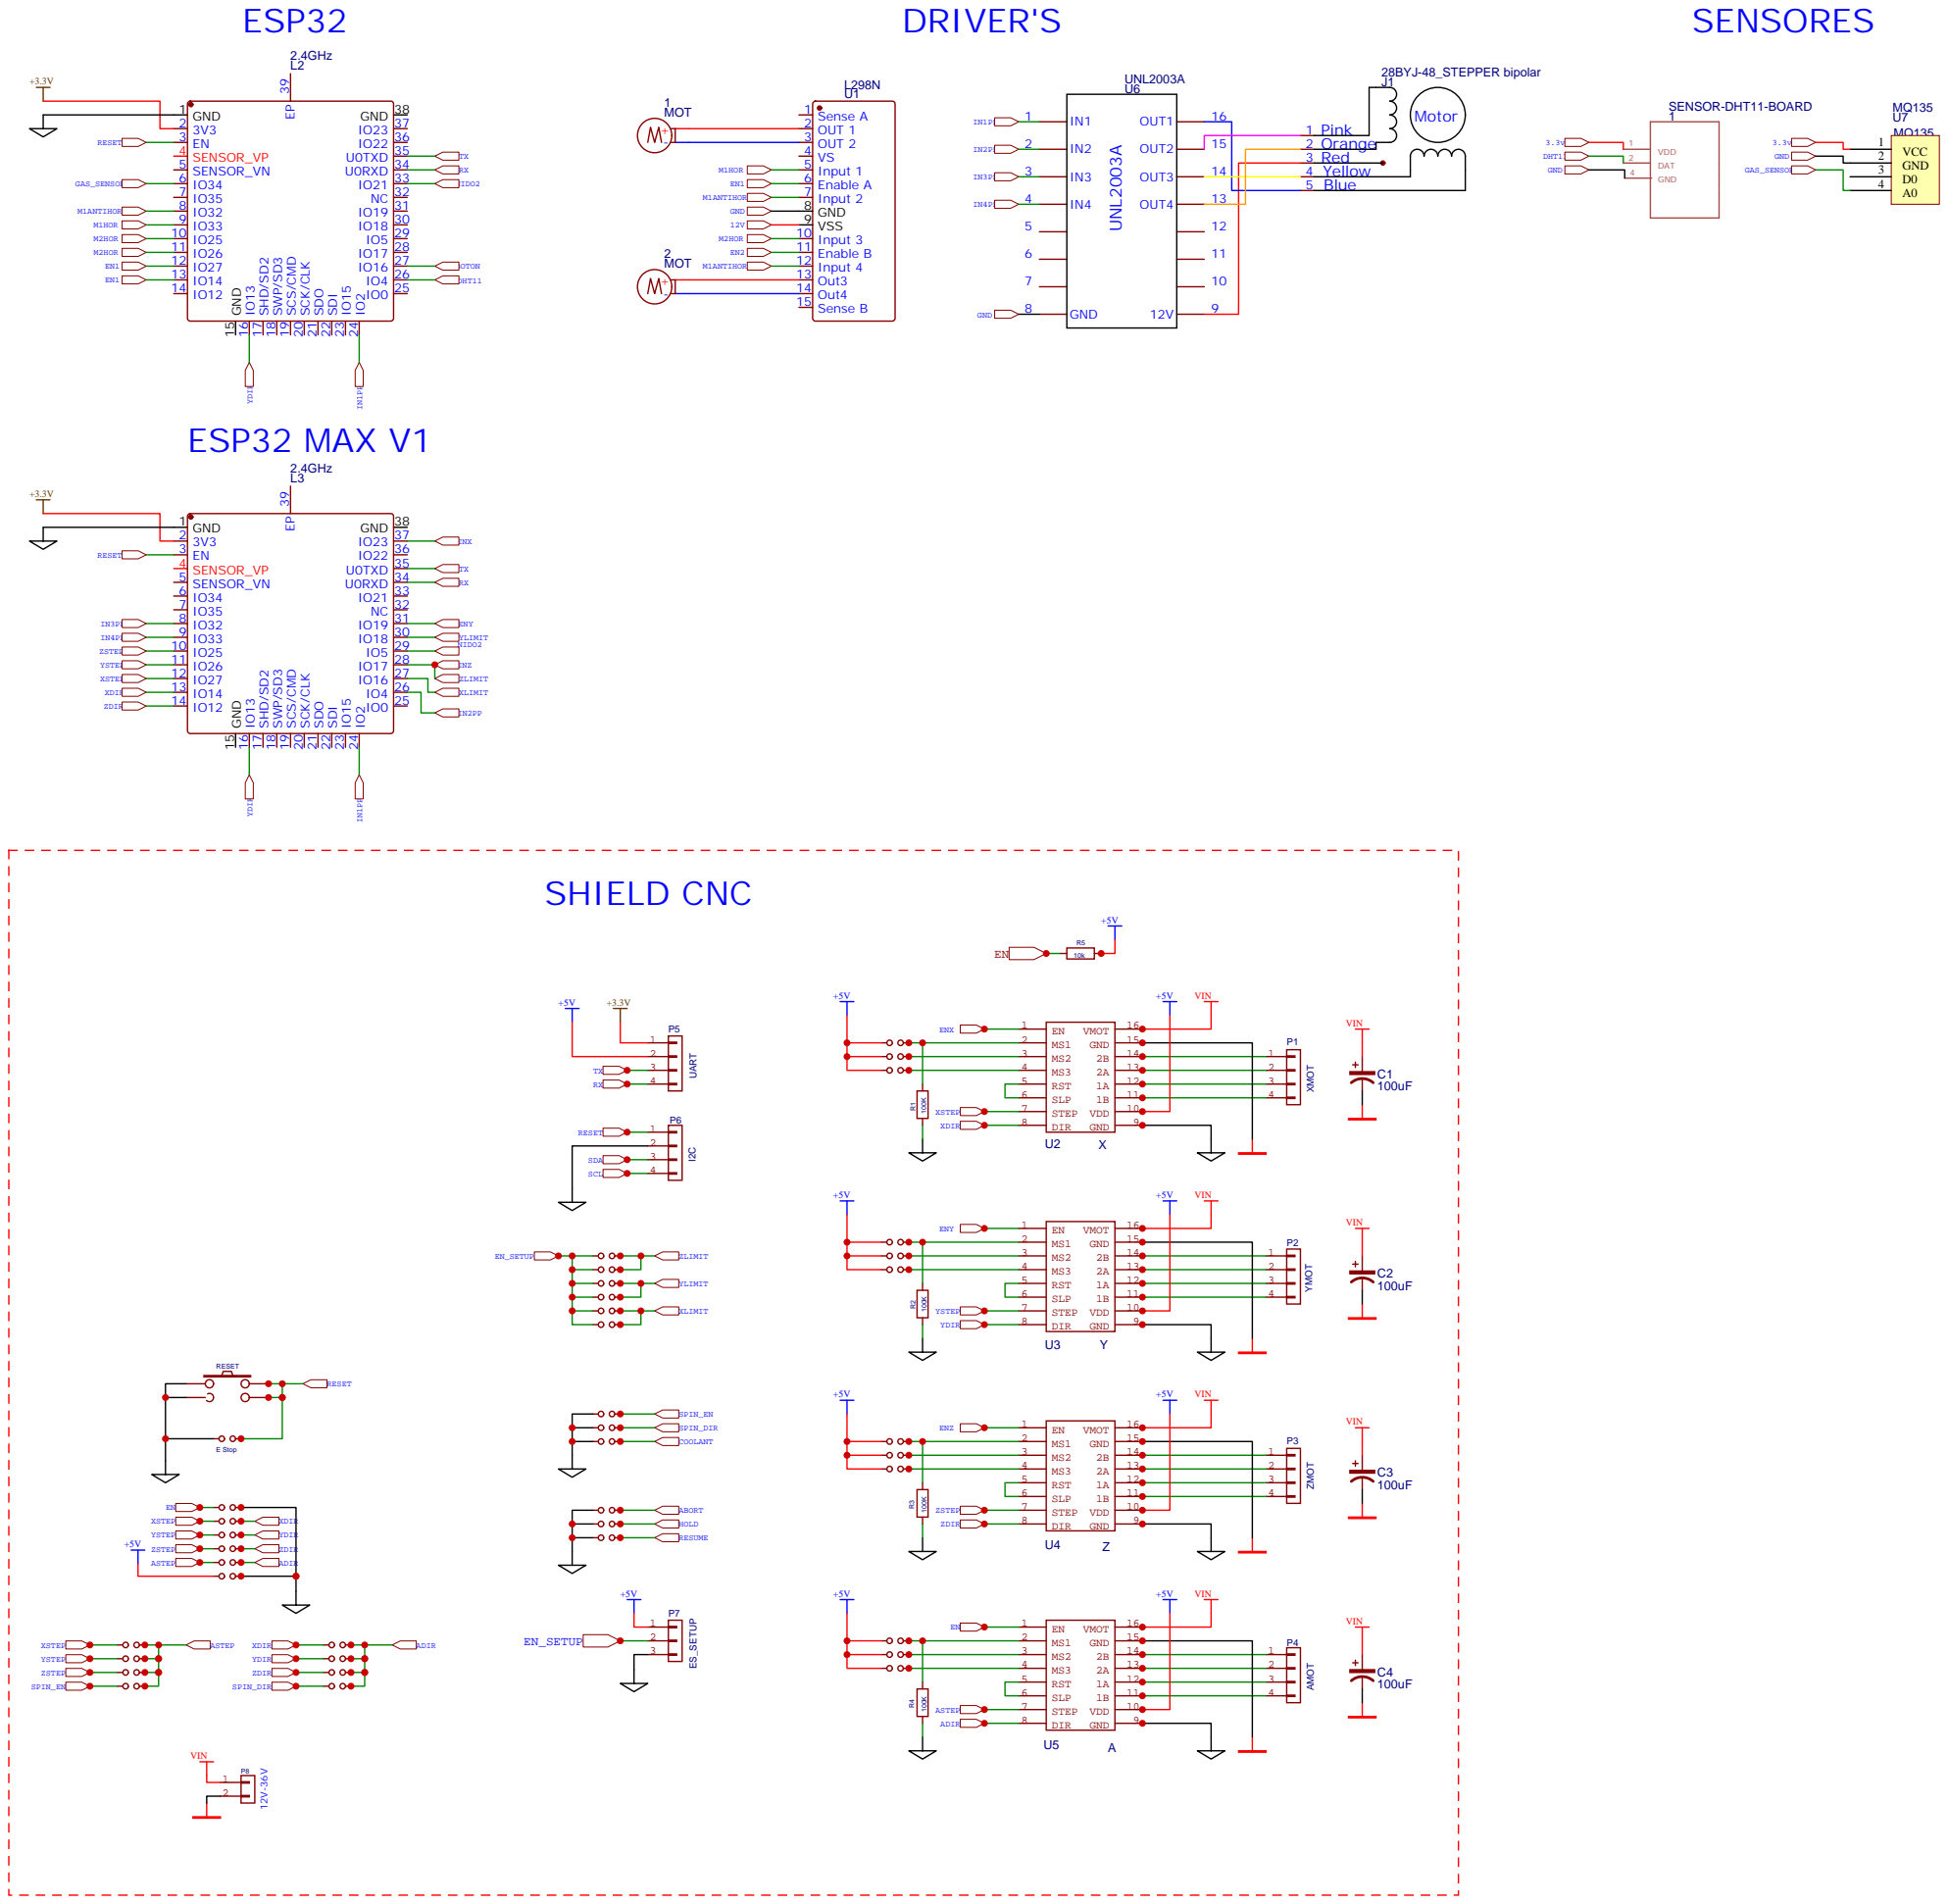
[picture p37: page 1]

IO2 24 IO15 23 SDI 22 SDO 21 SCK/CLK 20 SCS/CMD 19 SWP/SD3 18 SHD/SD2 17 IO13 16 GND 15

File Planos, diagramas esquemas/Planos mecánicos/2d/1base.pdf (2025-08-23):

E E

F F

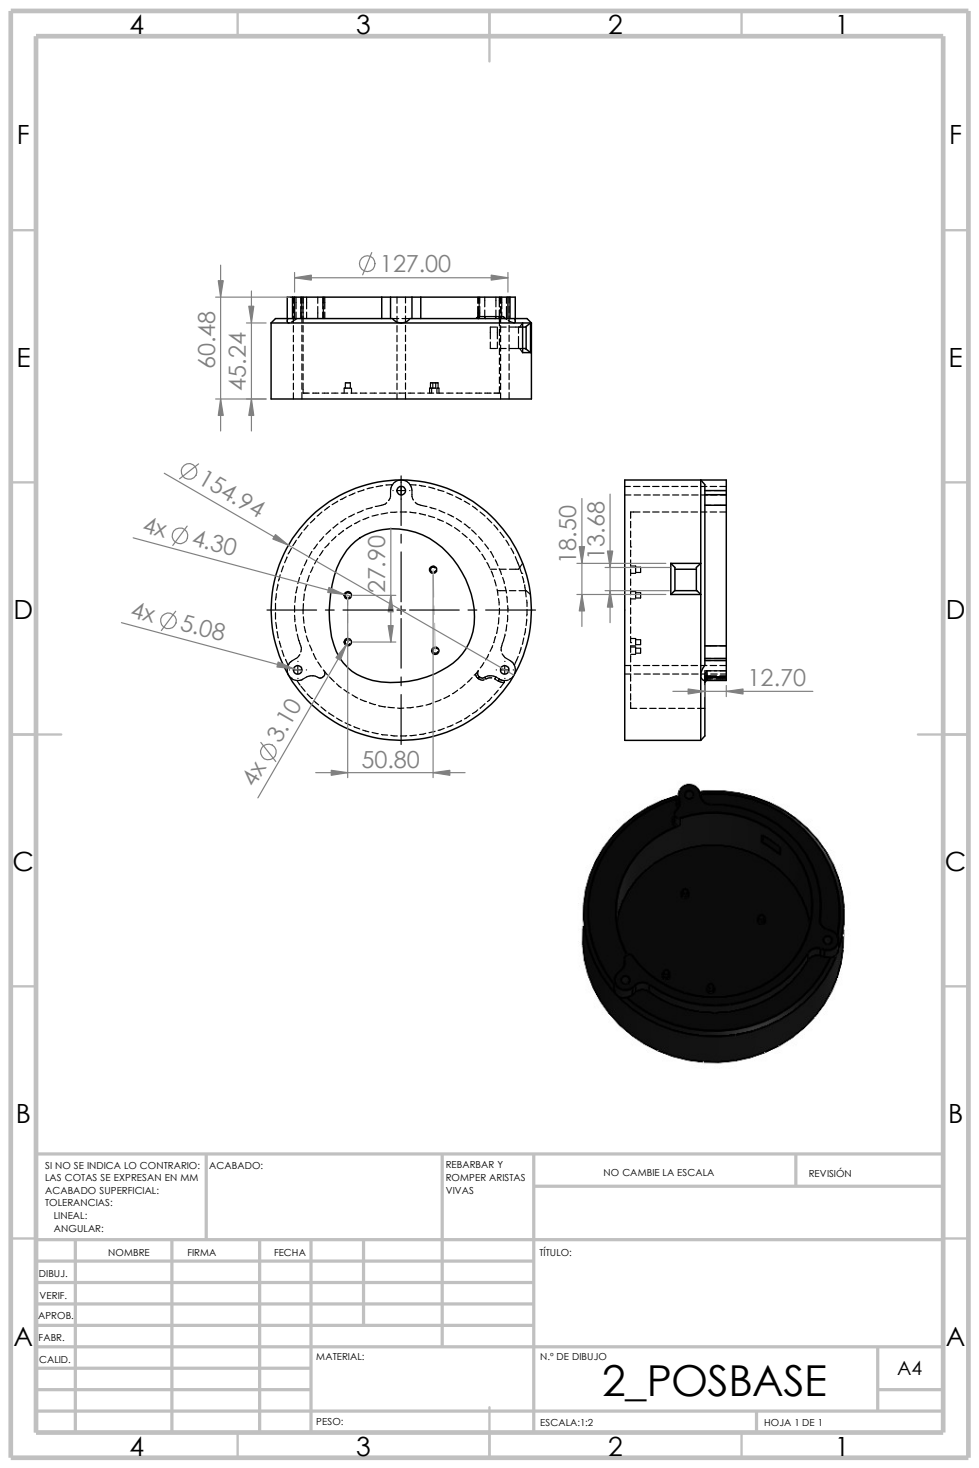
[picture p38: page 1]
MATERIAL:; REVISIÓN; N.º DE DIBUJO; ESCALA:1:2; HOJA 1 DE 1; PESO:; VIVAS; FABR.; CALID.; SI NO SE INDICA LO CONTRARIO:; ACABADO:; REBARBAR Y ROMPER ARISTAS; 2_POSBASE ¹³.68 18.50

LAS COTAS SE EXPRESAN EN MM
ACABADO SUPERFICIAL:
TOLERANCIAS:
LINEAL:
ANGULAR:

NO CAMBIE LA ESCALA

NOMBRE | FIRMA | FECHA | TÍTULO:

DIBUJ.

VERIF.
APROB.

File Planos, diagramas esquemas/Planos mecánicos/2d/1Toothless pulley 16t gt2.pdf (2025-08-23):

E E

F F

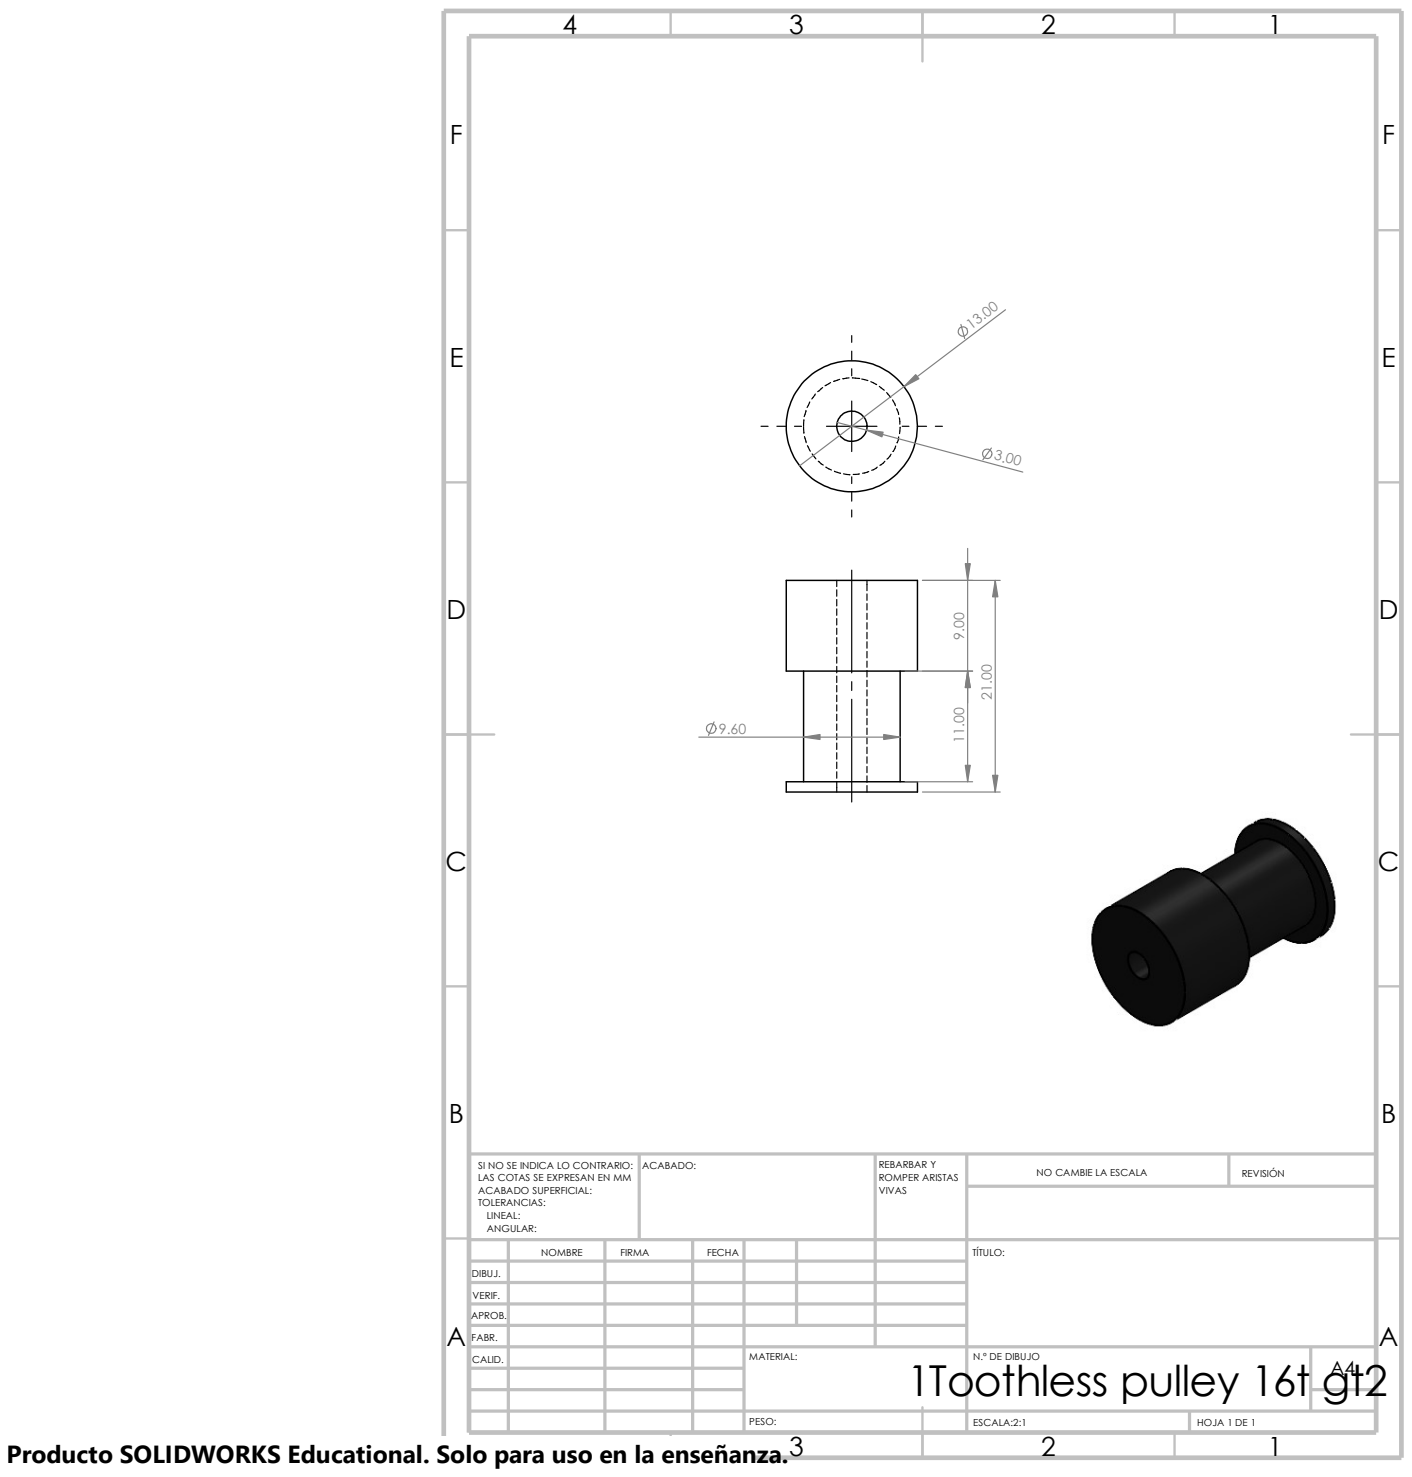
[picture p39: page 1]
ESCALA:2:1; PESO:; N.º DE DIBUJO; HOJA 1 DE 1; NO CAMBIE LA ESCALA; REVISIÓN; FABR.; CALID.; ACABADO:; VIVAS; MATERIAL:; REBARBAR Y ROMPER ARISTAS; 1Toothless pulley 16t gt2

SI NO SE INDICA LO CONTRARIO:
LAS COTAS SE EXPRESAN EN MM
ACABADO SUPERFICIAL:
TOLERANCIAS:
LINEAL:
ANGULAR:

NOMBRE | FIRMA | FECHA | TÍTULO:

DIBUJ.

VERIF.
APROB.

Producto SOLIDWORKS Educational. Solo para uso en la enseñanza.

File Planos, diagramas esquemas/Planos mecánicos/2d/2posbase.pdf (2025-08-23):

E E

F F

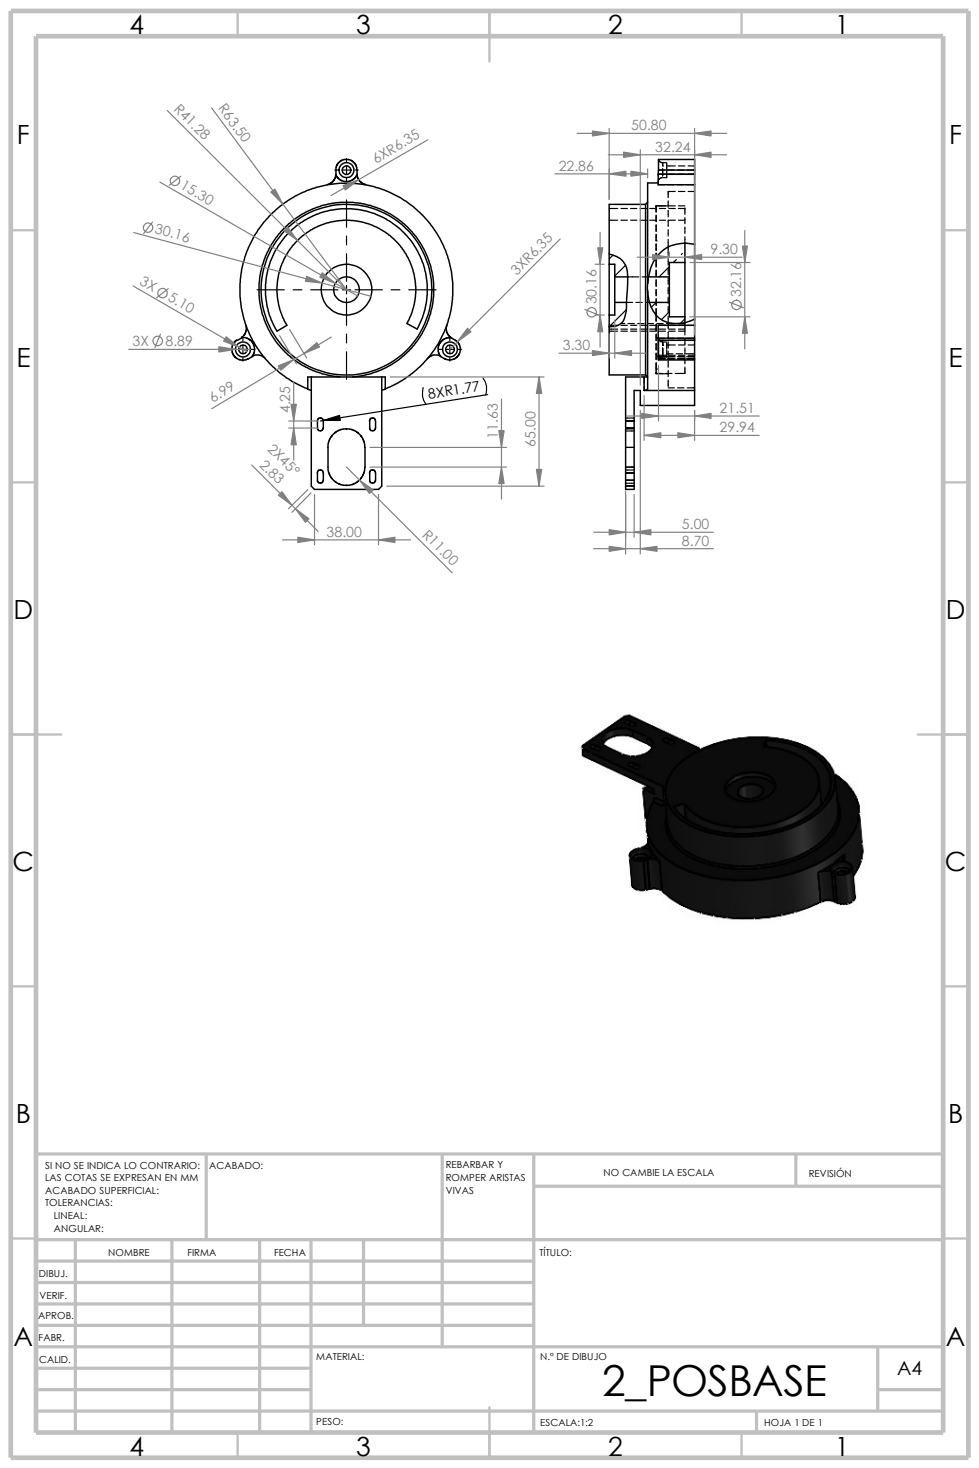
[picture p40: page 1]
HOJA 1 DE 1; PESO:; N.º DE DIBUJO; ESCALA:1:2; NO CAMBIE LA ESCALA; REVISIÓN; MATERIAL:; FABR.; CALID.; ACABADO:; VIVAS; REBARBAR Y ROMPER ARISTAS; 2_POSBASE

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

NOMBRE | FIRMA | FECHA | TÍTULO:

DIBUJ.

VERIF.
APROB.

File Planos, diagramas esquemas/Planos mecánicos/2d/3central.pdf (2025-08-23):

E E

F F

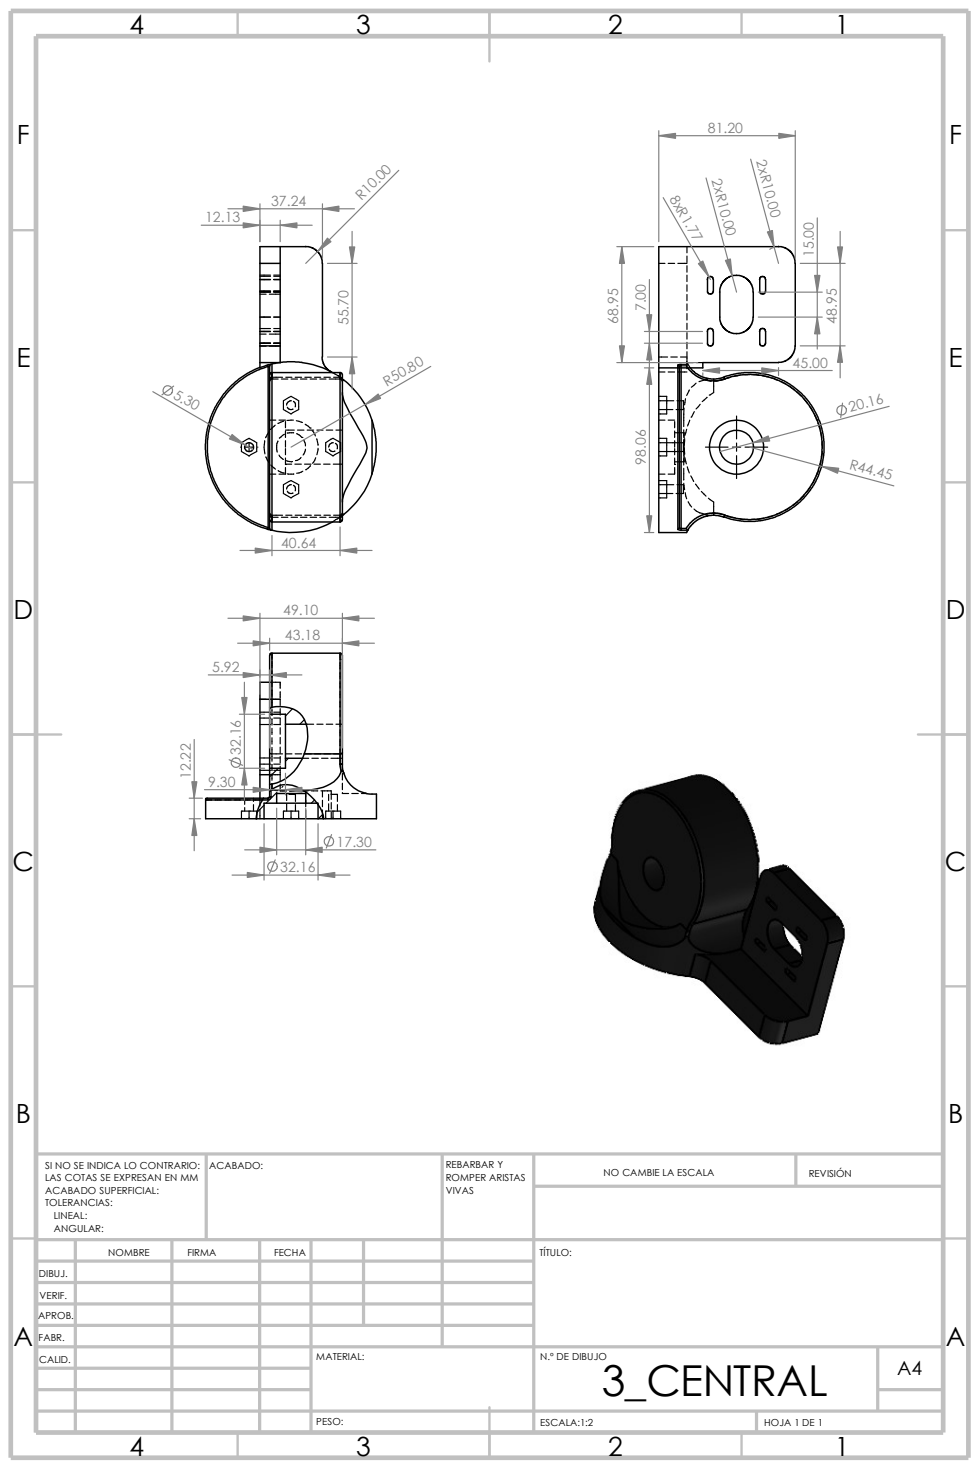
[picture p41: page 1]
N.º DE DIBUJO; ESCALA:1:2; HOJA 1 DE 1; PESO:; REVISIÓN; MATERIAL:; FABR.; CALID.; ACABADO:; VIVAS; REBARBAR Y ROMPER ARISTAS; 3_CENTRAL ³².16 12.22

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

NO CAMBIE LA ESCALA

NOMBRE | FIRMA | FECHA | TÍTULO:

DIBUJ.

VERIF.
APROB.

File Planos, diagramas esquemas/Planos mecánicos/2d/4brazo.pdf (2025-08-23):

E E

F F

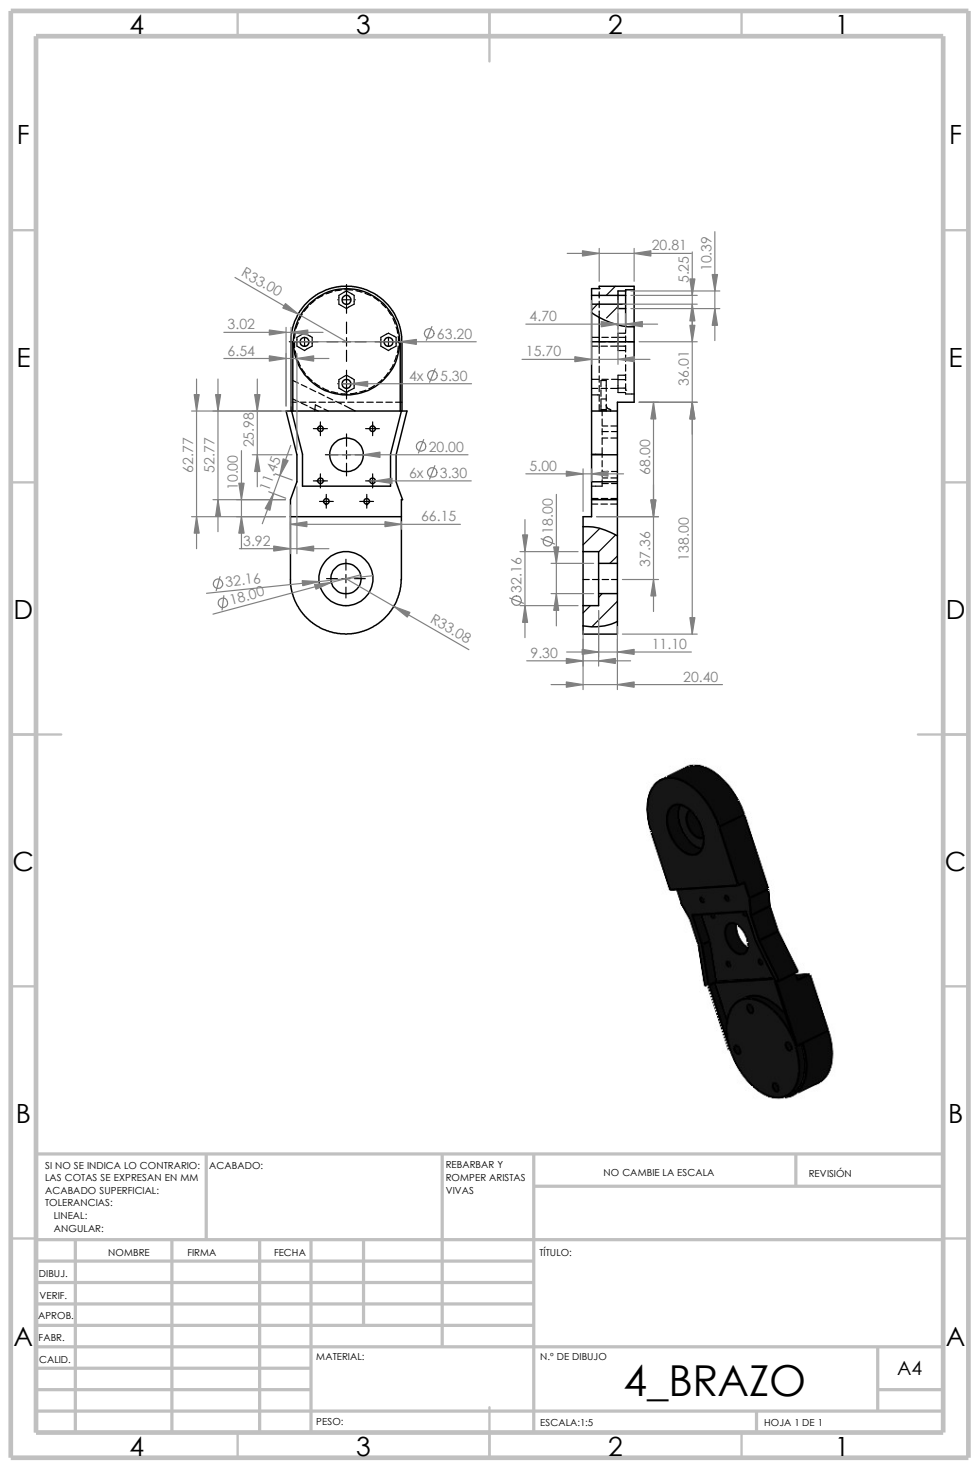
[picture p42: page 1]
MATERIAL:; N.º DE DIBUJO; ESCALA:1:5; HOJA 1 DE 1; PESO:; NO CAMBIE LA ESCALA; REVISIÓN; FABR.; CALID.; ACABADO:; VIVAS; REBARBAR Y ROMPER ARISTAS; 4_BRAZO

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

NOMBRE | FIRMA | FECHA | TÍTULO:

DIBUJ.

VERIF.
APROB.

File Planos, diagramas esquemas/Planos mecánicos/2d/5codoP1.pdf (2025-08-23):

E E

F F

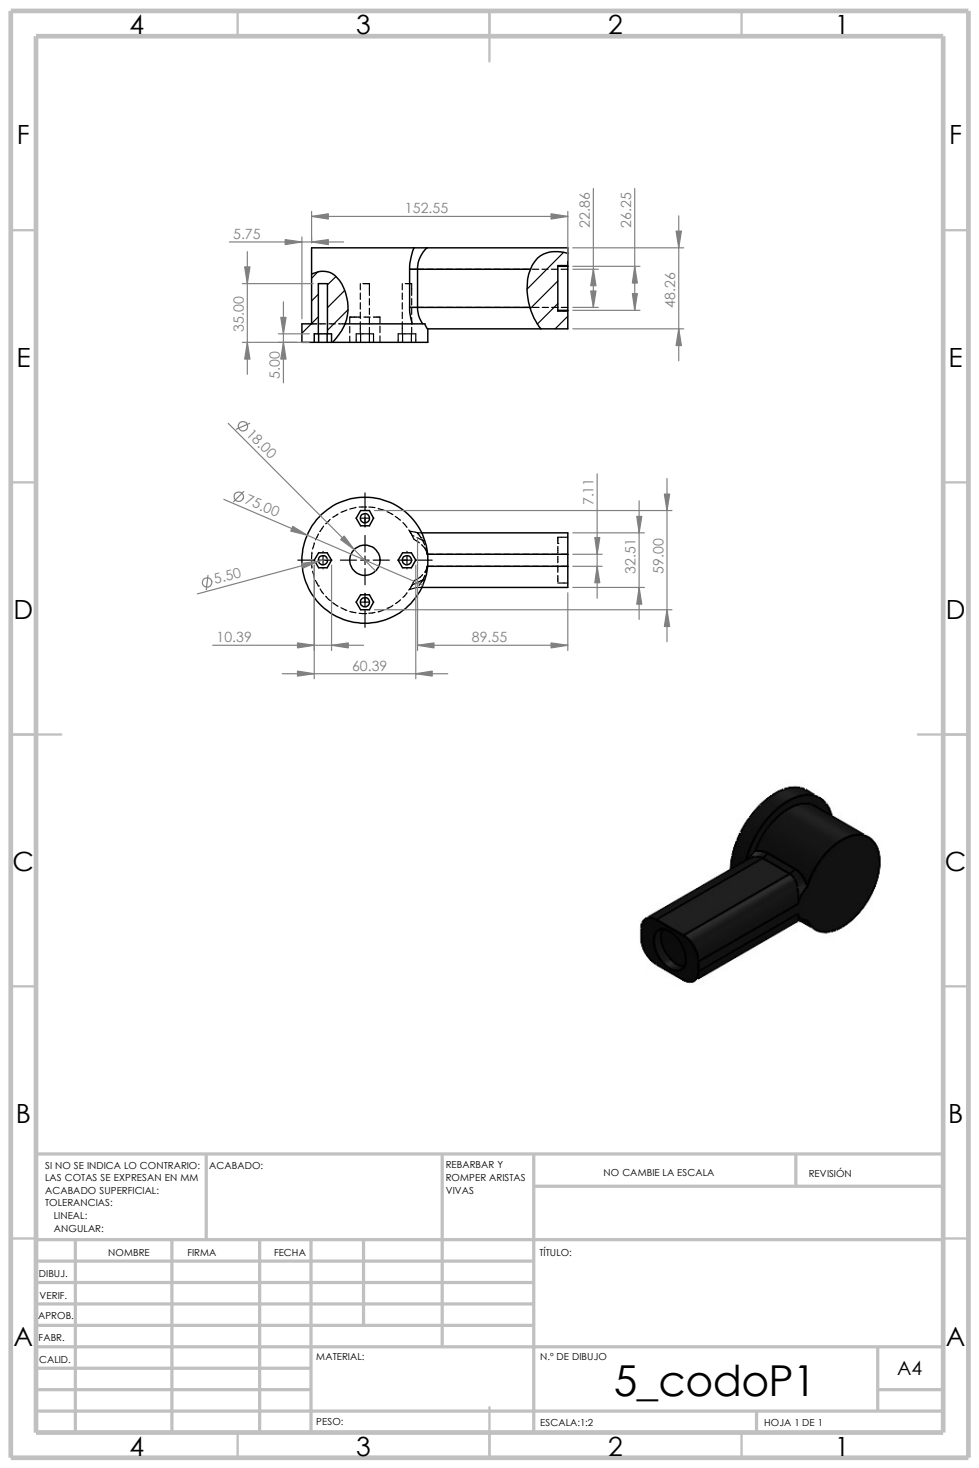
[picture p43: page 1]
ESCALA:1:2; PESO:; N.º DE DIBUJO; HOJA 1 DE 1; NO CAMBIE LA ESCALA; REVISIÓN; FABR.; CALID.; ACABADO:; VIVAS; MATERIAL:; REBARBAR Y ROMPER ARISTAS; 5_codoP1

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

NOMBRE | FIRMA | FECHA | TÍTULO:

DIBUJ.

VERIF.
APROB.

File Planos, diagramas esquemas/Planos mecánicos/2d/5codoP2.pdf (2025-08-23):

E E

F F

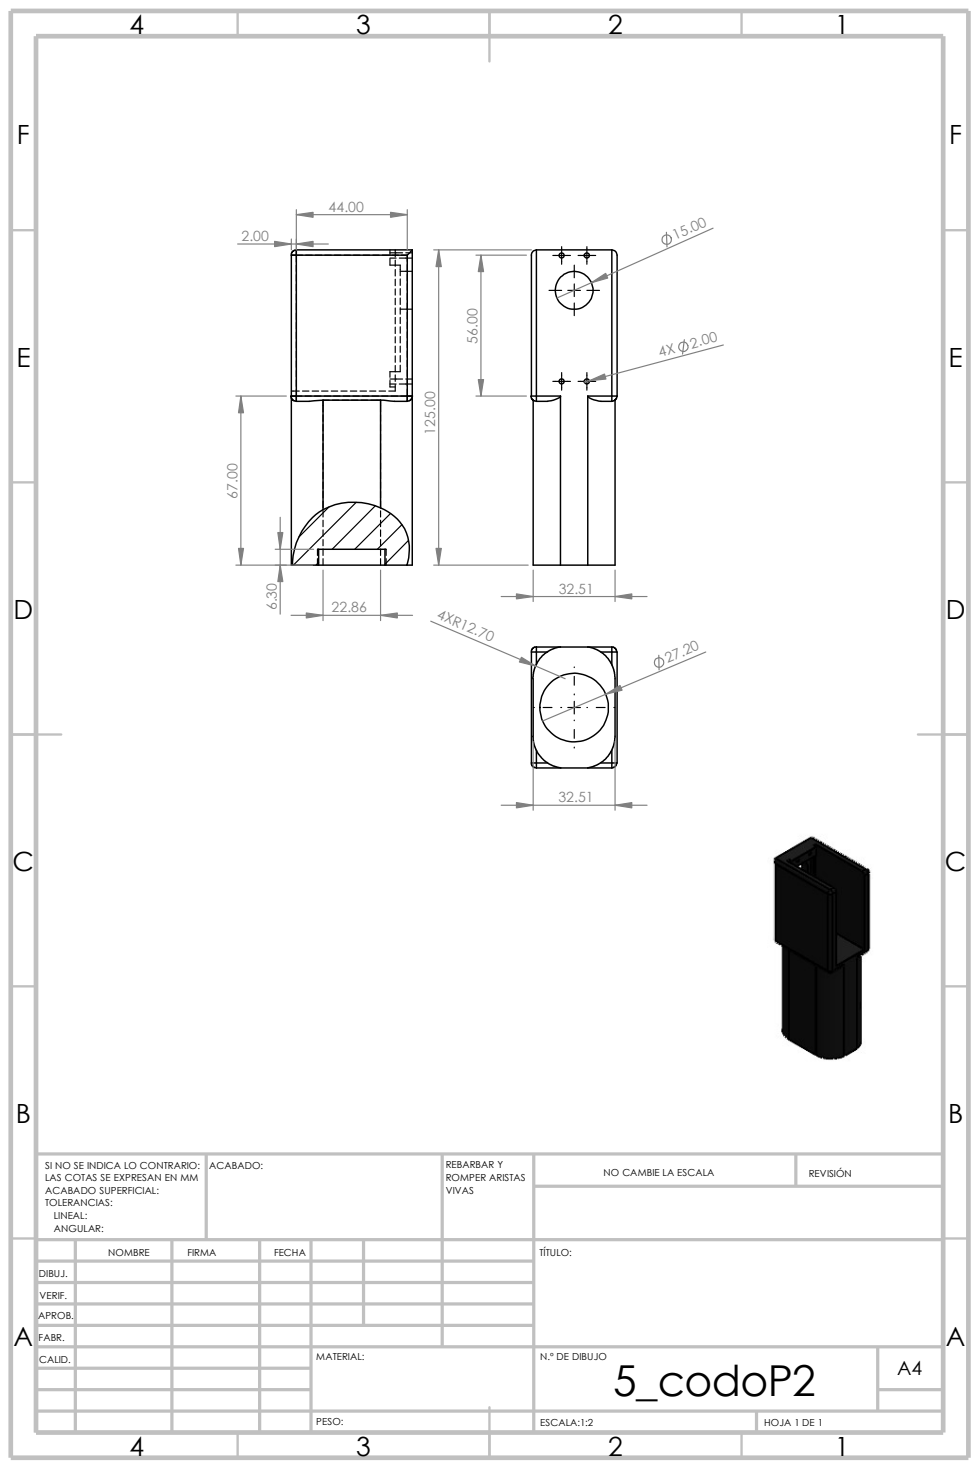
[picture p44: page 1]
PESO:; FABR.; ESCALA:1:2; HOJA 1 DE 1; N.º DE DIBUJO; REVISIÓN; CALID.; ACABADO:; VIVAS; MATERIAL:; REBARBAR Y ROMPER ARISTAS; 5_codoP2

NO CAMBIE LA ESCALA SI NO SE INDICA LO CONTRARIO:
LAS COTAS SE EXPRESAN EN MM
ACABADO SUPERFICIAL:
TOLERANCIAS:
LINEAL:
ANGULAR:

NOMBRE | FIRMA | FECHA | TÍTULO:

DIBUJ.

VERIF.
APROB.

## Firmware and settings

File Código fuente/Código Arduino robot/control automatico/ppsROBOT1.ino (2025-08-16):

#include <WiFi.h>
#include <PubSubClient.h>
#include <ArduinoJson.h>
#include <DHT.h>

///////////////MQTT/////////////////
const char* ssid = "RICARDO";
const char* password = "ofea5555";
const char* mqtt_server = "192.168.141.204";
const char* aut_topic = "casa/salon/automatico";
const char* foto = "casa/salon/foto";
const char* Temperature_topic = "casa/salon/temperatura";
const char* humidity_topic = "casa/salon/humedad";
const char* gas_topic = "casa/salon/gas";
const char* high_temp_topic = "falla/alta_temperatura";
const char* high_hum_topic = "falla/alta_humedad";
const char* high_gas_topic = "falla/alta_gas";
const char* nidos_topic = "casa/salon/nidosrecorridos";
const char* con_topic = "casa/salon/conteohuevos"; 
const char* nido2_topic = "casa/salon/conteohuevos"; 

//////////////////// sensor DHT11 ////////////////////////
#define DHTPIN 4       // Pin donde está conectado el DHT11
#define DHTTYPE DHT11  // Librería tipo de sensor DHT11
const int sensorPin1 = 5; // Define el pin del sensor
// Pines para Motor 1 y conexión L298N
#define PIN_IN1   33 
#define PIN_IN2   32 
#define PIN_ENA   14 
// Pines para Motor 2 y conexión L298N
#define PIN2_IN1  25 
#define PIN2_IN2  26 
#define PIN2_ENA  27 
// PWM 
#define MIN_PWM_SPEED 73  //ajustar pwm mín
#define MAX_PWM_SPEED 75 //ajustar pwm máx
////deginción de pines
int gas_sensor = 34;   
const int botonPin = 16;
const int NIDO2 = 21; //Entrada para habilitar nidos

// Configuración del sensor de gas más calibración
float m = -0.3523;        // Pendiente de la curva de calibración
float b = 0.714;          // Intersección de la curva de calibración
float R0 = 60;            // Valor inicial de R0 calculado
float sensorValue;
float sensor_volt; 
float RS_gas;
float ratio;
double ppm_log;
double ppm;

// Ajustes de calibración de temperaturas
float tempOffset = -1.0; 
float humOffset = -36.0;  
// Leer humedad y temperatura
float humedad;
float temperatura; 


unsigned long tiempoAnterior = 0;  //  el último tiempo
const unsigned long intervalo = 1000; //   segundos
unsigned long ultimoIntento = 0;

// Estados
bool automaticoActivo = false; // Esta variable se actualizará con el botón y con MQTT
bool automaticoActivo2 = false;
bool esperandoFoto = false;
unsigned long tiempoDeteccion = 0;
const unsigned long esperaFoto = 1000;

bool activacionNido1 = false;
unsigned long tiempoInicioNido1 = 0;
const unsigned long esperaNido1 = 900; //original 900
// estado de los motores por botón
bool motoresEncendidosPorBoton = false;
// Variable para el control del botón 
bool botonPresionadoPreviamente = false;
//contar nidos
int contadorNidos = 0;
bool estadoAnteriorSensor = HIGH;
unsigned long tiempoInicioLOW = 0;
const unsigned long tiempoMinimoLOW = 5000;  // ms
//pulsador manual
bool estadoNIDOs = false; // Estado actual apagado


WiFiClient espClient;
PubSubClient client(espClient);
DHT dht(DHTPIN, DHTTYPE);
void setup_wifi() {
  delay(10);
  Serial.println();
  Serial.print("Conectando a ");
  Serial.println(ssid);

  WiFi.begin(ssid, password);
  while (WiFi.status() != WL_CONNECTED) {
    delay(500);
    Serial.print(".");
  }

  Serial.println("\nWiFi conectado");
  Serial.print("Dirección IP: ");
  Serial.println(WiFi.localIP());
}

void reconnect() {
  while (!client.connected()) {
    Serial.print("Intentando conectar a MQTT...");
    String clientId = "ESP32Client-";
    clientId += String(random(0xffff), HEX);

    if (client.connect(clientId.c_str())) {
      Serial.println("conectado");

      // Suscribirse al tópico de posición
      client.subscribe(aut_topic);
      client.subscribe(esp2P_topic);
      client.subscribe(con_topic);
      client.subscribe(nido2_topic);
    } else {
      Serial.print("Fallido, rc=");
      Serial.print(client.state());
      Serial.println(" Intentar de nuevo en 5 segundos...");
      delay(5000);
    }
  }
}

void callback(char* topic, byte* message, unsigned int length) {
  Serial.print("Mensaje recibido en tópico: ");
  Serial.println(topic);

  String messageTemp;

  for (int i = 0; i < length; i++) {
    messageTemp += (char)message[i];
  }
  Serial.print("Mensaje: ");
  Serial.println(messageTemp);

  // Control automático desde MQTT
    if (String(topic) == aut_topic) {
      if (messageTemp == "OFF") {
        automaticoActivo = false;
        Serial.println("automático desactivado por MQTT"); 
        detenerMotor(PIN_ENA);
        detenerMotor(PIN2_ENA);
        motoresEncendidosPorBoton = false; // estado del botón
     }  else if (messageTemp == "ON") {
        automaticoActivo = true;
        Serial.println("automático activado por MQTT.");
        activarMotor(PIN_IN1, PIN_IN2, PIN_ENA, HIGH, MAX_PWM_SPEED);
        activarMotor(PIN2_IN1, PIN2_IN2, PIN2_ENA, HIGH, MAX_PWM_SPEED);
        motoresEncendidosPorBoton = true; // estado del botón
       }
    }
    if (String(topic) == con_topic || String(topic) == nido2_topic ) {
      if (messageTemp == "Huevos detectados: 0" || messageTemp == "nido2") {
        Serial.println("No hay Huevos, volver al nivel 0 || nido2");
        if (digitalRead(sensorPin1) == LOW) { 
          activarMotor(PIN_IN1, PIN_IN2, PIN_ENA, HIGH, MAX_PWM_SPEED);
          activarMotor(PIN2_IN1, PIN2_IN2, PIN2_ENA, HIGH, MAX_PWM_SPEED);
          }
          activacionNido1 = true;
          tiempoInicioNido1 = millis();
        }
      }
}


void setup() {
  Serial.begin(115200);
  // Configuración de pines 
  pinMode(PIN_IN1, OUTPUT);
  pinMode(PIN_IN2, OUTPUT);
  pinMode(PIN_ENA, OUTPUT);
  pinMode(botonPin, INPUT_PULLUP); // pull-up interno
  pinMode(PIN2_IN1, OUTPUT);
  pinMode(PIN2_IN2, OUTPUT);
  pinMode(PIN2_ENA, OUTPUT);
  pinMode(sensorPin1, INPUT); 
  pinMode(NIDO2, INPUT);
  setup_wifi();
  client.setServer(mqtt_server, 1883);
  client.setCallback(callback);
  contadorNidos = 0;
}

void loop() {
  //  conexión MQTT activa
  if (!client.connected()) {
      reconnect();
    }
  client.loop();
  //botón automático
  int estadoBoton = digitalRead(botonPin);
  // flanco de bajada
  if (estadoBoton == LOW && !botonPresionadoPreviamente) {
    delay(50); //anti-rebote inicial
    motoresEncendidosPorBoton = !motoresEncendidosPorBoton;

    if (motoresEncendidosPorBoton || automaticoActivo) {
      Serial.println("Botón presionado - Motores ENCENDIDOS (retención)");
      activarMotor(PIN_IN1, PIN_IN2, PIN_ENA, HIGH, MAX_PWM_SPEED);   // Motor 1 activar
      activarMotor(PIN2_IN1, PIN2_IN2, PIN2_ENA, HIGH, MAX_PWM_SPEED); // Motor 2 activar
      automaticoActivo = true; 
      Serial.println("Modo automático activado por botón.");
    } else {
      Serial.println("Botón presionado - Motores APAGADOS (retención)");
      detenerMotor(PIN_ENA);   // Detener Motor 1
      detenerMotor(PIN2_ENA);  // Detener Motor 2
      Serial.println("Modo automático desactivado por botón.");
    }
    botonPresionadoPreviamente = true;
  }
  else if (estadoBoton == HIGH && botonPresionadoPreviamente) {
    botonPresionadoPreviamente = false; 
    delay(50);
  }
    // Lógica automática activación desde panel node-red
  if (automaticoActivo && !esperandoFoto) {
    if (digitalRead(sensorPin1) == LOW) {
      detenerMotor(PIN_ENA);   // Detener Motor 1
      detenerMotor(PIN2_ENA);  // Detener Motor 2
      automaticoActivo = false;
      esperandoFoto = true;
      tiempoDeteccion = millis();
    }
  }
      // Lógica automática despues de pasar el nido 1
  if (automaticoActivo2 && !esperandoFoto) {
    if (digitalRead(sensorPin1) == LOW) {
      detenerMotor(PIN_ENA);   // Detener Motor 1
      detenerMotor(PIN2_ENA);  // Detener Motor 2
      automaticoActivo2 = false;
      esperandoFoto = true;
      tiempoDeteccion = millis();
    }
  }
  if (esperandoFoto && millis() - tiempoDeteccion >= esperaFoto) {
    client.publish(foto, "ON");
    esperandoFoto = false;
  }

  unsigned long tiempoActual = millis();
    // Ejecutar la función cada 3 segundos
  if (tiempoActual - tiempoAnterior >= intervalo) {
    tiempoAnterior = tiempoActual;
    sensores(); // leer sensores
}
  if (digitalRead(NIDO2) == HIGH ) {
    Serial.println("nido2");
    // Publicar en mqtt ir al siguiente nido
    String mensaje = String("nido2");
    client.publish(nido2_topic, mensaje.c_str());
  }

 //contador de nidos
  bool estadoActual = digitalRead(sensorPin1);
  if (estadoActual == LOW && estadoAnteriorSensor == HIGH  ) {
    tiempoInicioLOW = millis();
  }
  if (estadoActual == LOW && (millis() - tiempoInicioLOW >= tiempoMinimoLOW)) {
    contadorNidos++;
    Serial.print("Nido detectado: ");
    Serial.println(contadorNidos);

    // Publicar en mqtt los nidos recorridos
    String mensaje = String(contadorNidos);
    client.publish(nidos_topic, mensaje.c_str());
    while (digitalRead(sensorPin1) == LOW) {
      delay(5);
    }
  }
}

// Función para activar motores
void activarMotor(int in1Pin, int in2Pin, int enaPin, int direccion, int velocidad) {
  int velocidad_ajustada = constrain(velocidad, MIN_PWM_SPEED, MAX_PWM_SPEED);

  if (direccion == HIGH) { 
    digitalWrite(in1Pin, HIGH);
    digitalWrite(in2Pin, LOW);
  } else {
    digitalWrite(in1Pin, LOW);
    digitalWrite(in2Pin, HIGH);
  }
  analogWrite(enaPin, velocidad_ajustada);
}

// Función para detener motores
void detenerMotor(int enaPin) {
  analogWrite(enaPin, 0); 
}
//sensores de temperatura, humedad, gas co2
void sensores(){
  humedad = dht.readHumidity() + humOffset;
  temperatura = dht.readTemperature() + tempOffset;
  // Publicar la temperatura y humedad
  String tempPayload = String(temperatura);
  client.publish(Temperature_topic, tempPayload.c_str());
  String humPayload = String(humedad);
  client.publish(humidity_topic, humPayload.c_str());

  // Verificar si la temperatura supera los 30°C enviar señal de adventencia
  if (temperatura > 30.0) {
    String highTempPayload = "Alerta: Alta temperatura detectada (" + tempPayload + "°C)";
    client.publish(high_temp_topic, highTempPayload.c_str());
  }

  // Verificar si la humedad supera los 70% enviar señal de advertencia
  if (humedad > 70.0) {
    String highHumPayload = "Alerta: Alta humedad detectada (" + humPayload + "%)";
    client.publish(high_hum_topic, highHumPayload.c_str());
  }

  // Leer y publicar el valor del sensor de gas
  sensorValue = analogRead(gas_sensor);
  sensor_volt = sensorValue * (5.0 / 4095.0);
  RS_gas = ((5.0 * 10.0) / sensor_volt) - 10.0;
  ratio = RS_gas / R0;
  ppm_log = (log10(ratio) - b) / m;
  ppm = pow(10, ppm_log);
  String gasPayload = String(ppm);
  client.publish(gas_topic, gasPayload.c_str());
  // Verificar si el gas supera los 3000 ppm enviar señal de advertencia
  if (ppm > 3000) {
    String highGasPayload = "Alerta: Alto contenido de gas detectado (" + gasPayload + " ppm)";
    client.publish(high_gas_topic, highGasPayload.c_str());
  }
}

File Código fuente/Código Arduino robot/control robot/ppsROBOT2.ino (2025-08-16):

#include <AccelStepper.h>
#include <WiFi.h>
#include <PubSubClient.h>
#include <ArduinoJson.h>

////////////MQTT//////////////
const char* ssid = "RICARDO";
const char* password = "ofea5555";
const char* mqtt_server = "192.168.141.204";
const char* coord_topic = "casa/salon/coordenadas";


// Pines motores ESP32MAX V1
const int stepX = 27, dirX = 14;
const int stepY = 26, dirY = 13;
const int stepZ = 25, dirZ = 12;

// Pines ENA
const int enPinx = 23;
const int enPiny = 19;
const int enPinz = 17;

// Sensores fin de carrera
const int sensorX = 16; 
const int sensorY = 18; 
const int sensorZ = 17; 
const int NIDO2 = 5;

//////// Motor PP gripper
#define IN1 2
#define IN2 4
#define IN3 32
#define IN4 33

int steps[8][4] = {
  {1, 0, 0, 0}, {1, 1, 0, 0}, {0, 1, 0, 0}, {0, 1, 1, 0},
  {0, 0, 1, 0}, {0, 0, 1, 1}, {0, 0, 0, 1}, {1, 0, 0, 1}
};
int vueltasDeseadas0 = 5;
const int pasosPorVuelta0 = 4096;
int pasosTotales0 = vueltasDeseadas0 * pasosPorVuelta0;
const int pasosPorVuelta1 = 200;
const int pasosPorVuelta23 = 1000;

const float offset2 = 40.0, offset3 = 55.0; //ángulos corregidos por condiciones mecánicas
float ultimoT1 = 0;
bool gripper = false;
bool nido2 = false;
AccelStepper motor1(AccelStepper::DRIVER, stepX, dirX);
AccelStepper motor2(AccelStepper::DRIVER, stepY, dirY);
AccelStepper motor3(AccelStepper::DRIVER, stepZ, dirZ);


WiFiClient espClient;
PubSubClient client(espClient);
void setup_wifi() {
  delay(10);
  Serial.println();
  Serial.print("Conectando a ");
  Serial.println(ssid);

  WiFi.begin(ssid, password);
  while (WiFi.status() != WL_CONNECTED) {
    delay(500);
    Serial.print(".");
  }

  Serial.println("\nWiFi conectado");
  Serial.print("Dirección IP: ");
  Serial.println(WiFi.localIP());
}

void reconnect() {
  while (!client.connected()) {
    Serial.print("Intentando conectar a MQTT...");
    String clientId = "ESP32Client-";
    clientId += String(random(0xffff), HEX);

    if (client.connect(clientId.c_str())) {
      Serial.println("conectado");

      // Suscribirse al tópico de posición
      client.subscribe(coord_topic);
    } else {
      Serial.print("Fallido, rc=");
      Serial.print(client.state());
      Serial.println(" Intentar de nuevo en 5 segundos...");
      delay(5000);
    }
  }
}
// Variables globales para los ángulos thetas123
float t1x = 0, t2y = 0, t3z = 0;

void callback(char* topic, byte* payload, unsigned int length) {
  String mensaje = "";
  for (int i = 0; i < length; i++) {
    mensaje += (char)payload[i];
  }
  mensaje.trim();

  if (String(topic) == coord_topic) {
    StaticJsonDocument<200> doc;
    DeserializationError error = deserializeJson(doc, mensaje);
    if (!error) {
      float theta1 = doc["theta1"].as<float>();
      float theta2 = doc["theta2"].as<float>();
      float theta3 = doc["theta3"].as<float>();
      t1x = theta1;
      t2y = theta2 - offset2;
      t3z = theta3 - offset3;
      ultimoT1 = t1x;
      moverA(t1x, t2y, t3z);
      delay(10);
      gripper = true;
    }
  }

}



void setup() {
  setup_wifi();
  client.setServer(mqtt_server, 1883);
  client.setCallback(callback);
  Serial.begin(115200);
  Serial.setTimeout(100);
  pinMode(NIDO2, OUTPUT);
  pinMode(enPinx, OUTPUT); digitalWrite(enPinx, LOW); //enPinx driver habilitados
  pinMode(enPiny, OUTPUT); digitalWrite(enPiny, LOW); //enPiny driver habilitados
  pinMode(enPinz, OUTPUT); digitalWrite(enPinz, LOW); //enPinz driver habilitados

  pinMode(sensorX, INPUT_PULLUP);
  pinMode(sensorY, INPUT_PULLUP);
  pinMode(sensorZ, INPUT_PULLUP);

  motor1.setAcceleration(100); motor1.setMaxSpeed(100);
  motor2.setAcceleration(300); motor2.setMaxSpeed(300);
  motor3.setAcceleration(300); motor3.setMaxSpeed(300);

  pinMode(IN1, OUTPUT);
  pinMode(IN2, OUTPUT);
  pinMode(IN3, OUTPUT);
  pinMode(IN4, OUTPUT);
  reconnect();
  hacerHoming();  // Al inicio se hace el homming para buscar el cero
}

void loop() {
  if (!client.connected()) {
    reconnect();
  }
  client.loop();
 //secuencia en cascada del movimiento del robot
  if (gripper) {
    activarGripperHorario();
    hacerHoming1();
    delay(5);
    volverACero0(285);
    // definir a 0° los motores
    motor1.setCurrentPosition(0);
    motor2.setCurrentPosition(0);
    motor3.setCurrentPosition(0);
    long pasos50 = 125.0 * pasosPorVuelta1 / 360.0;
    motor1.moveTo(pasos50);
    while (motor1.distanceToGo() != 0) motor1.run();
    volverACero12(-130, 0);
    activarGripperAntiHorario();
    hacerHomingYZ(); //este es hacer homming de dos ejesYZ
    delay(5);
    hacerHoming();
    digitalWrite(NIDO2, HIGH);
    delay(900);
    digitalWrite(NIDO2, LOW);
    gripper = false;
  }
}


//Mover motores
void moverA(float t1x, float t2y, float t3z) {
  long p1 = t1x * pasosPorVuelta1 / 360.0;
  long p2 = t2y * pasosPorVuelta23 / 360.0;
  long p3 = t3z * pasosPorVuelta23 / 360.0;
  motor1.moveTo(p1);
  motor2.moveTo(p2);
  motor3.moveTo(p3);
  while (motor1.distanceToGo() != 0 || motor2.distanceToGo() != 0 || motor3.distanceToGo() != 0) {
    motor1.run(); motor2.run(); motor3.run();
  }
}

void volverACero0(float p11){
  long p21 = p11 * pasosPorVuelta1 / 360.0;
  motor1.moveTo(p21);
  while (motor1.distanceToGo() != 0) motor1.run();
}
void volverACero12(float p12, float p13) {
  long p22 = p12 * pasosPorVuelta23 / 360.0;
  long p23 = p13 * pasosPorVuelta23 / 360.0;
  motor2.moveTo(p22);
  while (motor2.distanceToGo() != 0) motor2.run();
  motor3.moveTo(p23);
  while (motor3.distanceToGo() != 0) motor3.run();
}
void volverACero1(float p11, float p12, float p13) {
  long p21 = p11 * pasosPorVuelta1 / 360.0;
  long p22 = p12 * pasosPorVuelta23 / 360.0;
  long p23 = p13 * pasosPorVuelta23 / 360.0;

  motor2.moveTo(p22);
  while (motor2.distanceToGo() != 0) motor2.run();
  motor3.moveTo(p23);
  while (motor3.distanceToGo() != 0) motor3.run();
  motor1.moveTo(p21);
  while (motor1.distanceToGo() != 0) motor1.run();
}

void hacerHoming() {
  Serial.println("Iniciando homing...");
  // Mover solo el eje X a +50° para encontrar el homming de seguridad 
  long pasos50 = 50.0 * pasosPorVuelta1 / 360.0;
  motor1.moveTo(pasos50);
  bool encontrado = false;
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
